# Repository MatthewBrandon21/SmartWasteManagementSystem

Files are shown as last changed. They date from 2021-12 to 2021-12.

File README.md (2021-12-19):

<h1 align="center">
  Smart Waste Management System (SWMS)
</h1>
<p align="center">
  Smart city waste management system for our Mobile Pervasive Computing course final project.
</p>

### Preview of this system
<p align="Center">
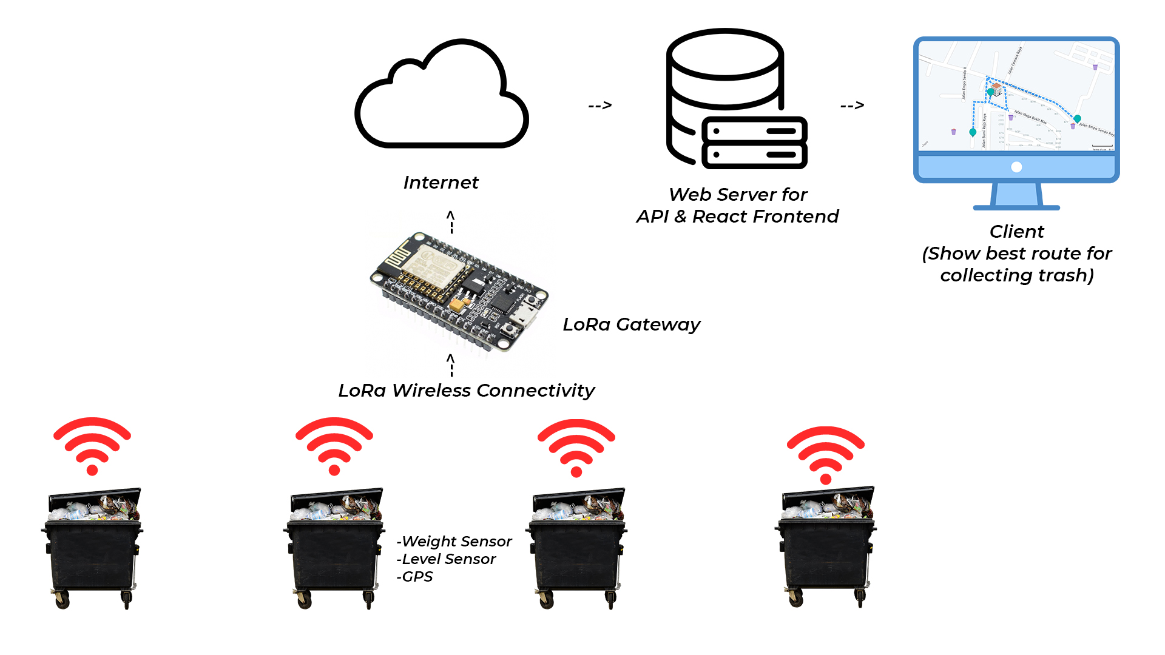
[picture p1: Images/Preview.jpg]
  
</p>

### General Architecture
<p align="Center">
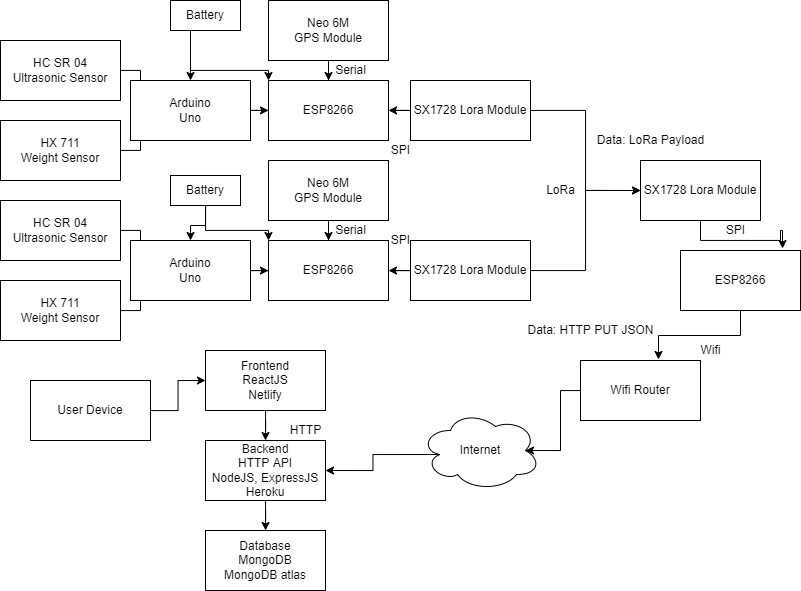
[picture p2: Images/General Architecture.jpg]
  
</p>

#

## How to make node device

### Hardware Architecture
<p align="Center">
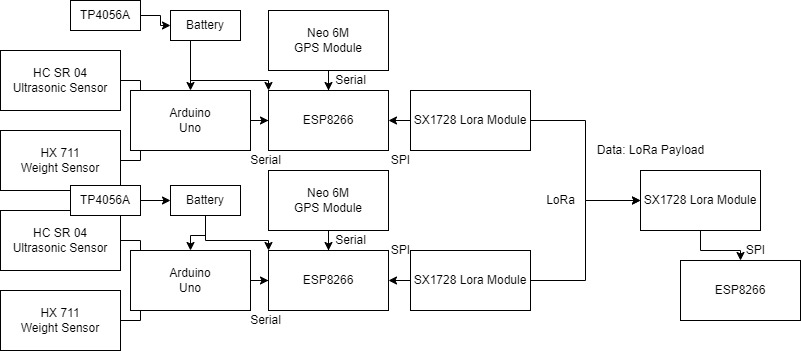
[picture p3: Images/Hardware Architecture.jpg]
  
</p>

### List of component
- Microcontroller ESP8266
- Microcontroller Arduino Uno
- Lora Module SX1278
- GPS Module Neo 6M
- Weight Sensor HX711+ 10kg Load cell
- Ultrasonic Sensor HC SR 04
- Servo SG40
- Battery 18650
- TP4056A

### List of component for gateway
- Microcontroller ESP8266
- Lora Module SX1278

Total budget (December 2021) = Rp. 356.200 (~ US $24,76)

### Component pin connection
1. Servo --> 
Orange : D3 (ESP8266),
Brown : GND (ESP8266),
Red : 3V3 (ESP8266)
2. Ultrasonic --> 
VCC : 5V (Arduino Uno),
Trig : Digital 5 (Arduino Uno),
Echo : Digital 6 (Arduino Uno),
GND : GND (Arduino Uno)
3. GPS --> 
GND : GND (ESP8266),
TX : D4 (ESP8266),
RX : D1 (ESP8266),
VCC : 3v3 (ESP8266)
4. HX711 --> 
VCC : 5V (Arduino Uno),
SCK : Digital 2 (Arduino Uno),
Data : Digital 3 (Arduino Uno),
GND : GND (Arduino Uno)
5. LoRa Wan --> 
GND : GND (ESP8266),
VCC : 3.3V (ESP8266),
NSS : D8 (ESP8266),
MOSI : D7 (ESP8266),
MISO : D6 (ESP8266),
CK : D5 (ESP8266),
RST : D0 (ESP8266),
DIO0 : D2 (ESP8266)
6. Serial Communication Arduino Uno and ESP8266 --> 
Digital 7 (Arduino Uno): TX (ESP8266),
Digital 8 (Arduino Uno): RX (ESP8266)

#

## How this work?
In this project, we use 2 microcontrollers, ESP8266 and Arduino Uno. The reason for using 2 microcontrollers simultaneously is because to supply power of weight sensor the HX711 module requires a larger current than the ESP8266 power regulator can provide. Therefore, if it is forced to run on esp8266, a bootloop will occur or it will restart continuously when the system boots. Arduino Uno's power regulator is larger than the ESP8266, therefore it can run the HX711 weight sensor module along with the ultrasonic sensor properly. But because we have implemented esp8266 in our prototype, we made it so that esp8266 and arduino uno can communicate to send sensor data. But if you want to save space, budget and efficiency, you can only use Arduino Uno.

For communication between the ESP8266 and Arduino Uno, use serial communication with a baud rate of 9600. Serial communication will happen every 3 seconds between Arduino Uno and Esp8266 to update esp8266 sensor data. And the lora frequency used is 915 MHz. To update data to API server will be done every 5 seconds by request by gateway. Then the gateway will request data one by one from the node so that data collisions do not occur (lora packet collosion -> for more details I have simulated packet collisions in LoRa communication which can be seen on).

For lora module with esp8266 using SPI communication protocol between the two. So the plot of Arduino Uno will send serial communication for weight sensor and Ultrasonic with plain text. Then it will be parsed by esp8266 in the trash, plus GPS data and the logic of whether the trash can is full or not by esp8266. And part of the value will be sent via Lora Payload to the esp8266 gateway. the gateway will parse the data sent by the node, and finally it will be generated as JSON to be sent HTTP PUT to the web API by the gateway.

<p align="Center">
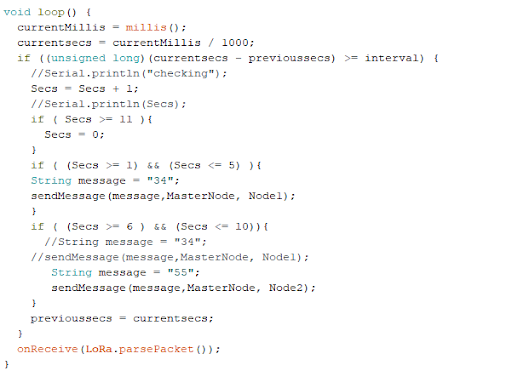
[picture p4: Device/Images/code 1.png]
  
</p>

So in the picture above, you can see the change in data retrieval requests and data updates to the API by the gateway. So in this example, seconds 1-5 will retrieve data from node 1 and seconds 6-10 will retrieve data from node 2.

#

## Final result
<p align="Center">
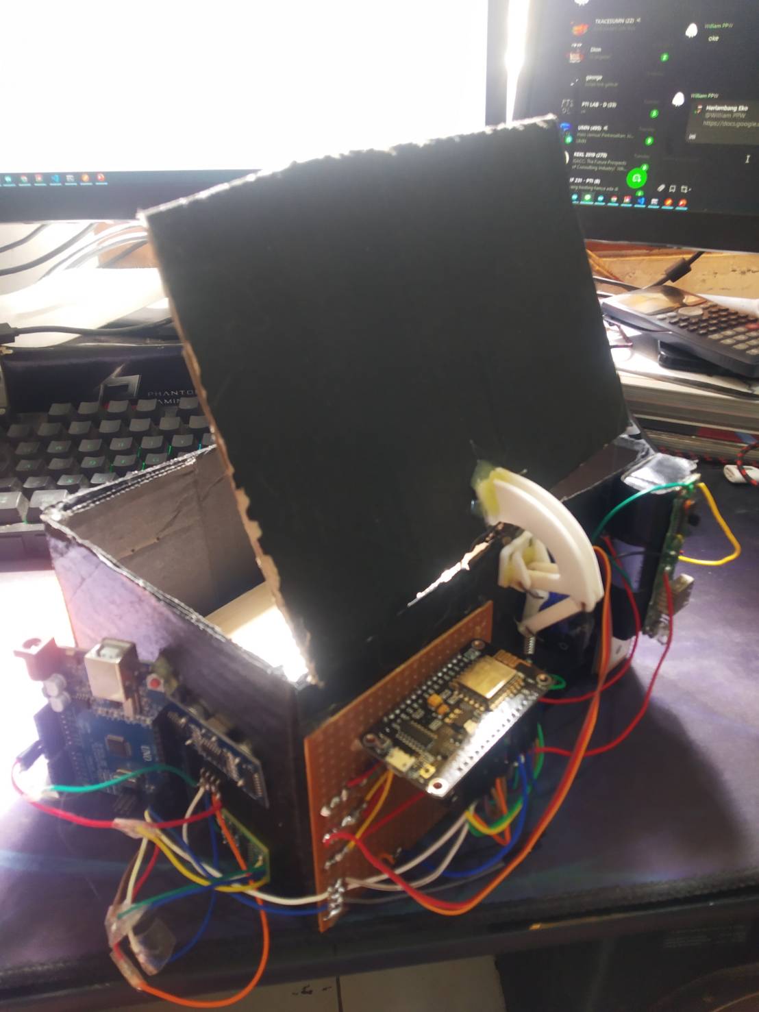
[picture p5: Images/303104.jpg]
  
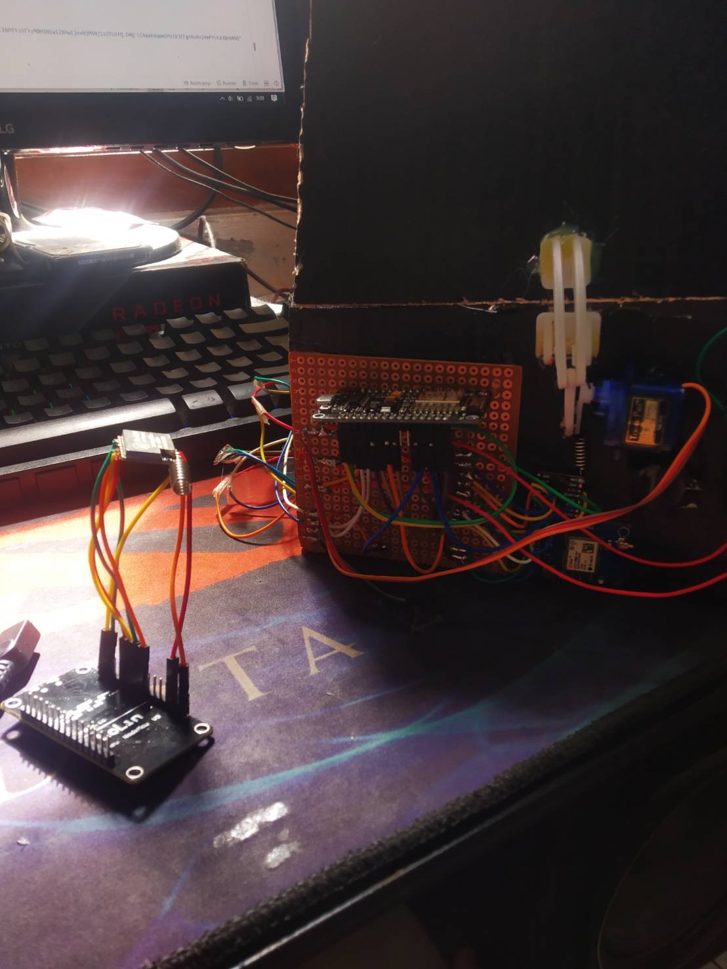
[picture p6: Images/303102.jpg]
  
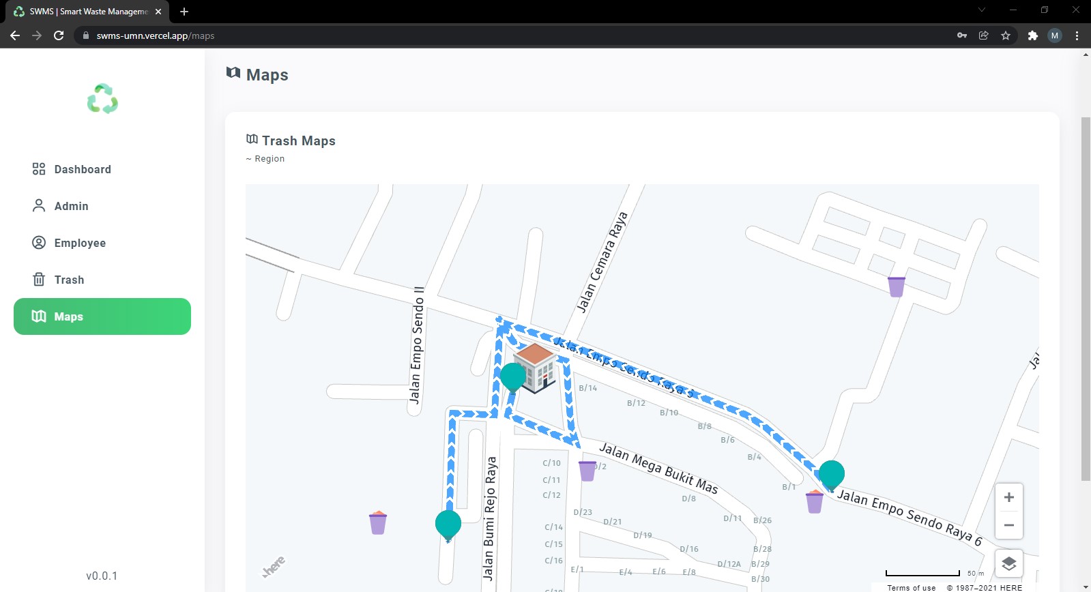
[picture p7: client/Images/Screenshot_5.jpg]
  
</p>

#

## <i>If need help, feel free to contact us! MatthewBrandon21 / rellpa.</i>

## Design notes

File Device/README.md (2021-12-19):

# Smart Waste Management System Arduino Code

We're using ESP8266
For some other controllers including controllers which are not ESP family, may need some more configuration.

#

## libraries
1. SPI.h
2. Lora.h
3. ESP8266WiFi.h
4. ESP8266HTTPClient.h
5. WiFiClient.h
6. TinyGPS++.h
7. SofwareSerial.h
8. Servo.h
9. HX711.h
10. stdlib.h

#

## How to use this project ?
If you want reverse engineering this project app:
- Install and open arduino IDE
- Install esp38266 board family, using board manager
- Clone and open "Arduino Uno.ino", "ESP8266 Gateway.ino", and "ESP8266 Node.ino"
- Configure URL of API Server on "ESP8266 Gateway.ino"
- Flash 3 ino file to seperate controller (Arduino Uno.ino --> arduino uno, ESP8266 Gateway.ino --> esp8266 gateway, etc)
- Done

#

## How this work?
In this project, we use 2 microcontrollers, ESP8266 and Arduino Uno. The reason for using 2 microcontrollers simultaneously is because to supply power of weight sensor the HX711 module requires a larger current than the ESP8266 power regulator can provide. Therefore, if it is forced to run on esp8266, a bootloop will occur or it will restart continuously when the system boots. Arduino Uno's power regulator is larger than the ESP8266, therefore it can run the HX711 weight sensor module along with the ultrasonic sensor properly. But because we have implemented esp8266 in our prototype, we made it so that esp8266 and arduino uno can communicate to send sensor data. But if you want to save space, budget and efficiency, you can only use Arduino Uno.

For communication between the ESP8266 and Arduino Uno, use serial communication with a baud rate of 9600. Serial communication will happen every 3 seconds between Arduino Uno and Esp8266 to update esp8266 sensor data. And the lora frequency used is 915 MHz. To update data to API server will be done every 5 seconds by request by gateway. Then the gateway will request data one by one from the node so that data collisions do not occur (lora packet collosion -> for more details I have simulated packet collisions in LoRa communication which can be seen on).

For lora module with esp8266 using SPI communication protocol between the two. So the plot of Arduino Uno will send serial communication for weight sensor and Ultrasonic with plain text. Then it will be parsed by esp8266 in the trash, plus GPS data and the logic of whether the trash can is full or not by esp8266. And part of the value will be sent via Lora Payload to the esp8266 gateway. the gateway will parse the data sent by the node, and finally it will be generated as JSON to be sent HTTP PUT to the web API by the gateway.

<p align="Center">
  
</p>

So in the picture above, you can see the change in data retrieval requests and data updates to the API by the gateway. So in this example, seconds 1-5 will retrieve data from node 1 and seconds 6-10 will retrieve data from node 2.

<i>if need help, feel free to contact us! MatthewBrandon21 / rellpa.</i>

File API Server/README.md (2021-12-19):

# Smart Waste Management System API
### <i>!!This app created using NodeJS and ExpressJS</i>

#

## Features:
- Store sensor data trash from node gateway to database
- Authentication user with JWT and have 2 user role (admin & employee, each user role have different privilege)
- CRUD user
- CRUD trashdata

#

## Library Dependencies
- @hapi/joi = Validation request input
- bcrypt.js = Hashing bcrypt algorithm
- cors = Middleware for ExpressJS for HTTP header based
- dotenv = Make and use .env file
- express.js = HTTP framwork for NodeJS
- jsonwebtoken = untuk authentukasi dan authorisasi
- mongoose = Framework to use MongoDB database
- nanoid = MongoDB ObjectID generator. Shortener objectID length.
- nodemon : Development tool for auto restarting NodeJS 

#

## Demo app:
You can access this demo API to https://smartwastemanagement-api.herokuapp.com/

#

## How to use this project ?
If you want reverse engineering this project app:
1. Clone this folder
2. Make MongoDB database with users and trashdatas collection (You can see example on JSON Database/ .json).
2. Set url mongoDB database in config/db.config.js
3. set port according to your system port availability in app.js 
4. Run npm install
5. Run npm run

How to use API:
1. You must register first, use register POST method
2. Login with account that you have created, use login POST method
3. In the login response there is a JWT token that will expire in 1 hour
4. Copy and paste that JWT token as POST method header, Header key named "auth-token" with value JWT token

<i>if need help, feel free to contact us! MatthewBrandon21 / rellpa.</i>

#

## API Documentation
Trash data API ( /trashdata):
- router.get("/",trashdata.findAll);  -> Get all trash data

- router.post("/", trashdata.create); -> Make new trash data (use json body on http request)

- router.get("/:id", trashdata.findOne); -> Get trash data by id

- router.put("/:id", trashdata.update); -> Update trash data by id (use json body on http request)

- router.delete("/:id",trashdata.delete); -> Delete trash data by id

API User :
- router.get("/", users.findAll); -> Get all users
 
- router.get("/:id", users.findOne); -> Get a user by id

- router.put("/:id", users.update); -> Update user by id (use json body on http request)
 
- router.delete("/:id", users.delete); -> Delete user by id
 
- router.post("/register", async (req, res) => { function goes here } -> Register user
 
- router.post("/login", async (req, res) => { function goes here } -> Login user

#

### <i>*For improvement<i/>
You can add authentication for device (ESP32 HTTP POST)

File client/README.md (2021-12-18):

# Smart Waste Management System Frontend
### <i>!!This app created using ReactJS and HERE Routing API</i>

#

## Features:
- Dashboard page
- Login page
- Responsive web page
- CRUD admin user
- CRUD employee user
- CRUD Trash
- Auto map routing based trash --> Using HERE Routing API

#

## Demo app:
You can access this demo web to https://swms-umn.vercel.app/
For demo account:
Admin--> email: william@gmail.com password: 12345678
Employee--> email: pervasif@gmail.com password: pervasifsukses

#

## How to use this project ?
If you want reverse engineering this project app:
1. Clone this folder
2. Set Smart Waste Management System API Server url in src/api/index.jsx
3. Run npm install
4. Run npm run

<i>if need help, feel free to contact us! MatthewBrandon21 / rellpa.</i>

#

## Some Screenshoot of this web
<p align="left">
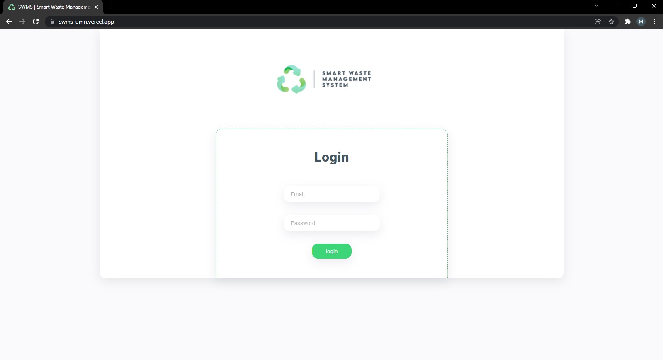
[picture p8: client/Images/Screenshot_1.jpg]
  
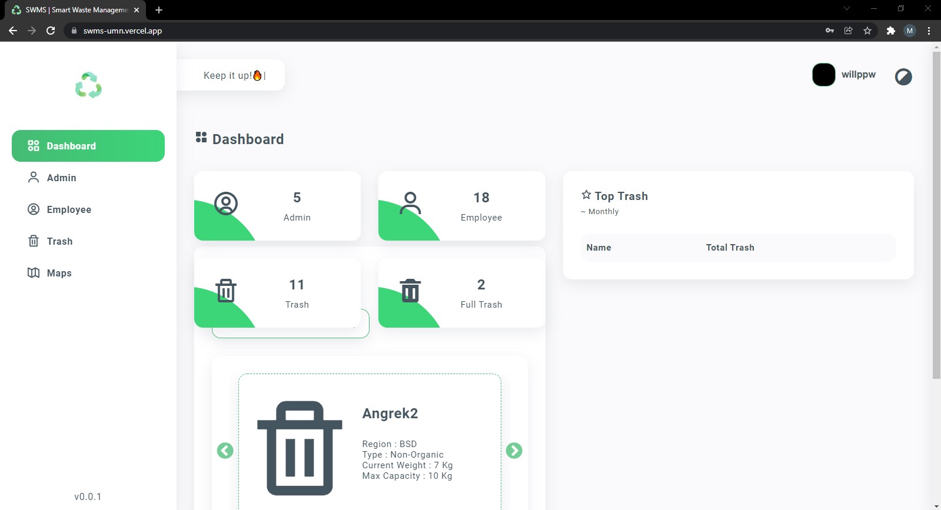
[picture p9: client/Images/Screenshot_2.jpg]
  
  
</p>

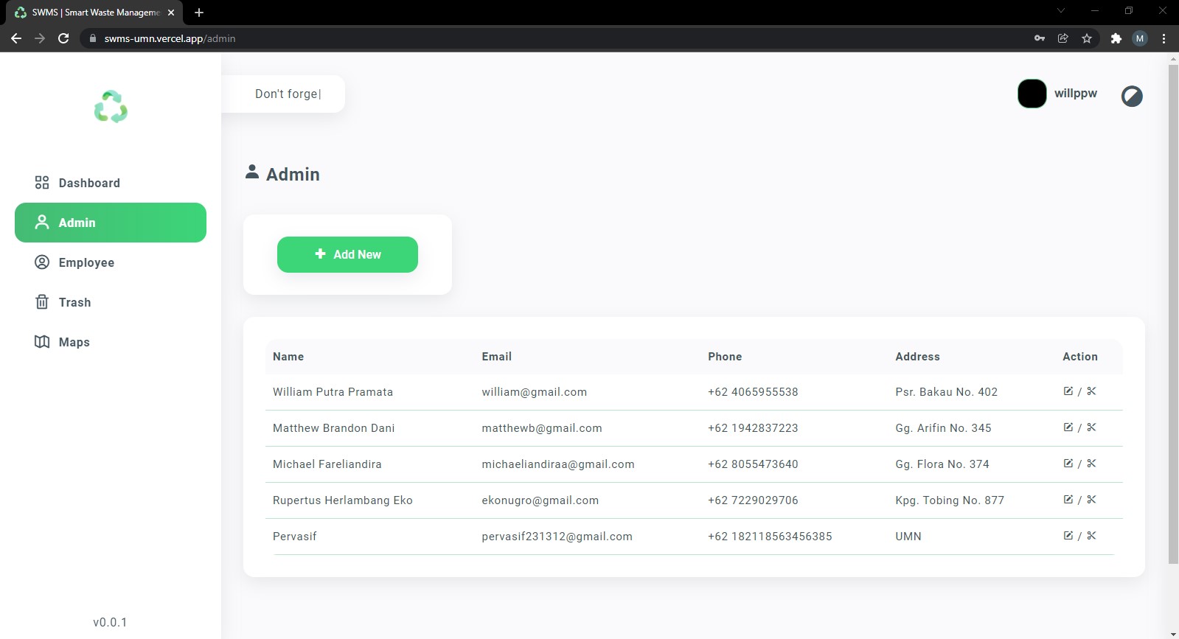
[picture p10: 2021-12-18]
client/Images/Screenshot_3.jpg

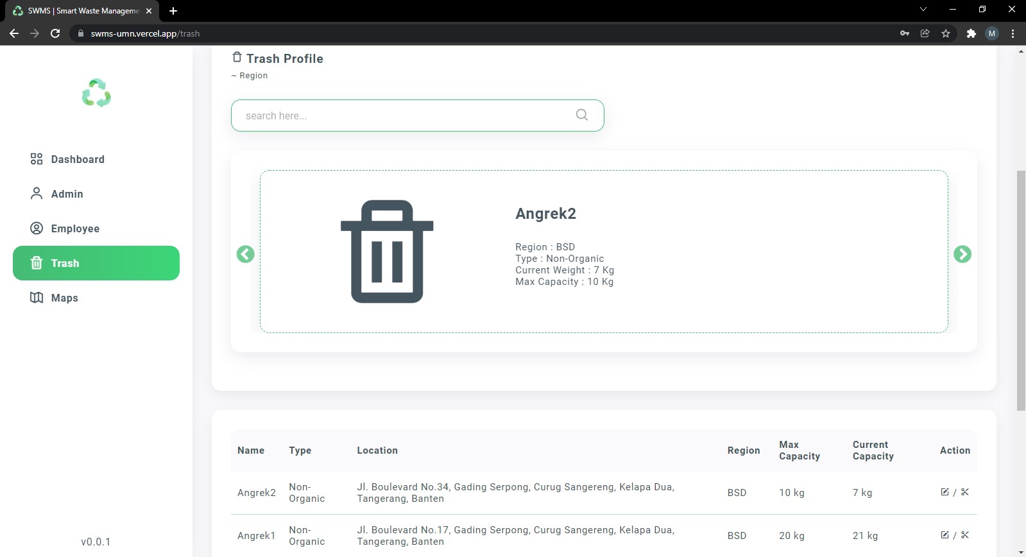
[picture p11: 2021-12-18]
client/Images/Screenshot_4.jpg

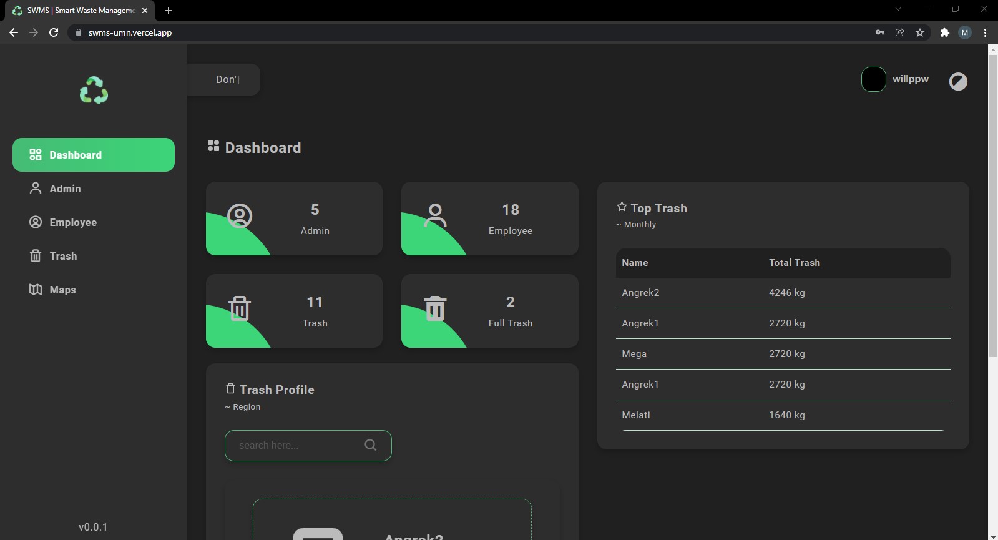
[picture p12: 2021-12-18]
client/Images/Screenshot_6.jpg

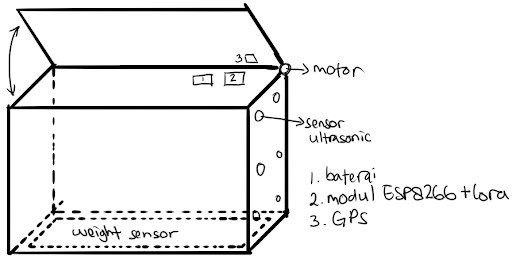
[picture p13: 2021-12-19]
Images/Plan.png

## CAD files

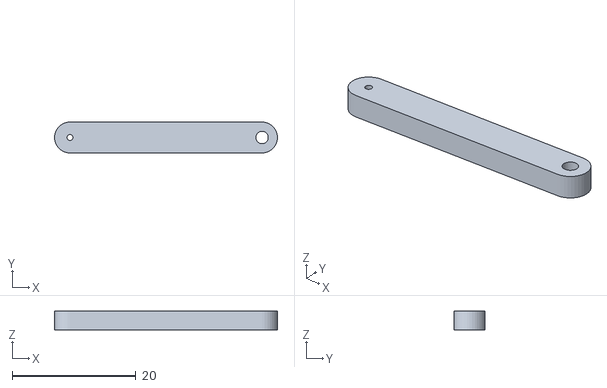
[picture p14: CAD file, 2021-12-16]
Device/3D Print for Servo Hinge/Push_Rod.STL
36.0 x 5.00 x 3.00

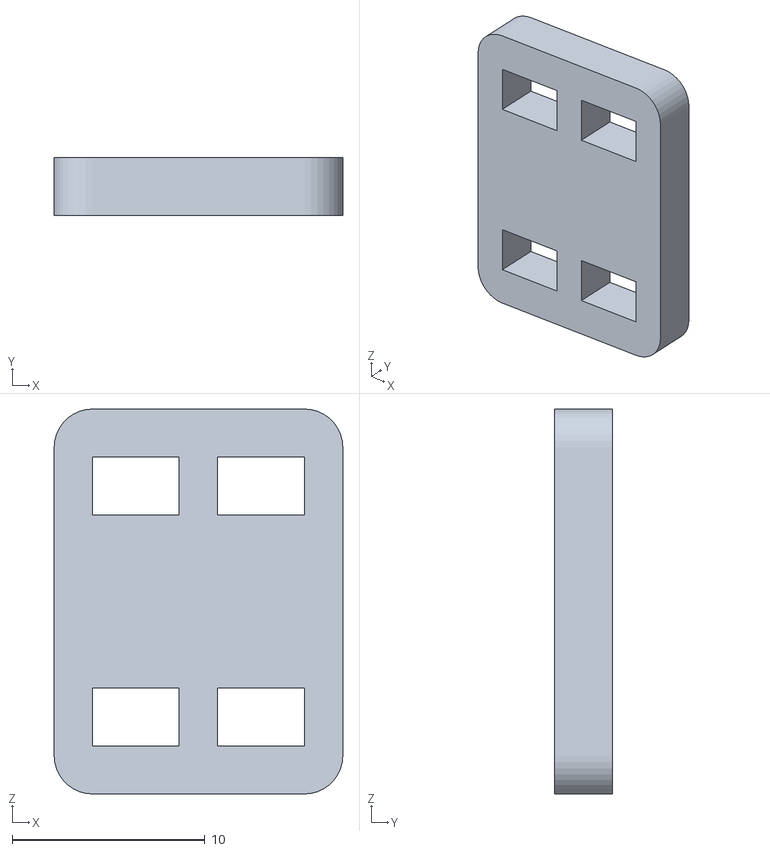
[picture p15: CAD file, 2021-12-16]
Device/3D Print for Servo Hinge/Hinge_Base.STL
15.0 x 3.00 x 20.0

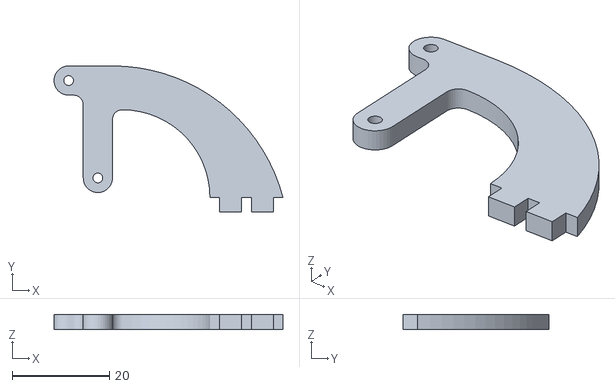
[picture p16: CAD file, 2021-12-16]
Device/3D Print for Servo Hinge/Horn.STL
47.0 x 30.0 x 3.00

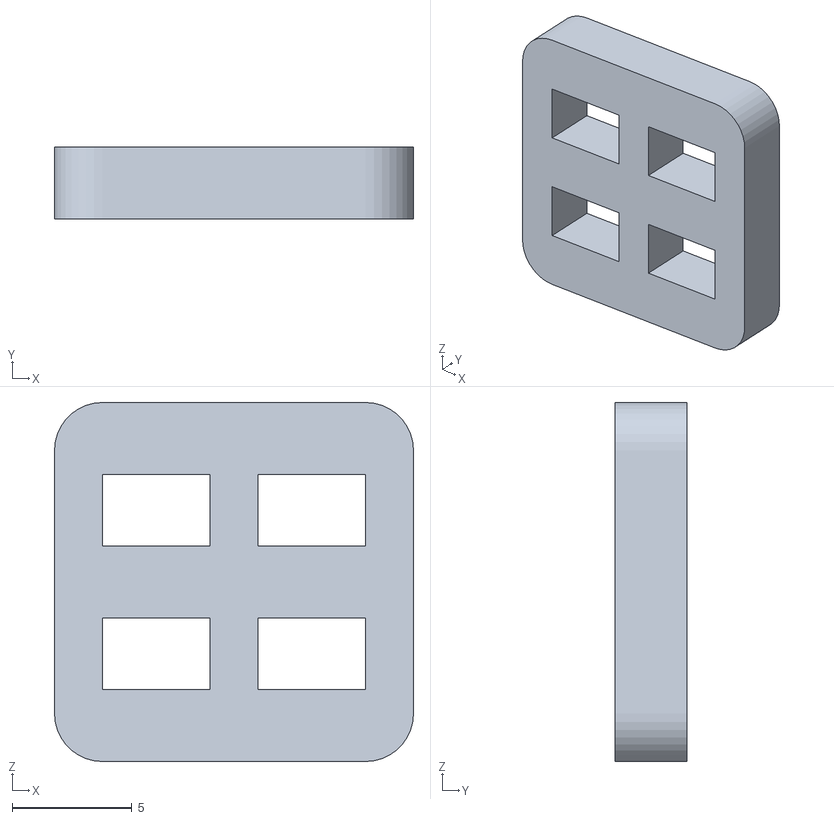
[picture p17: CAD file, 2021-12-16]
Device/3D Print for Servo Hinge/Horn_Base.STL
15.0 x 3.00 x 15.0

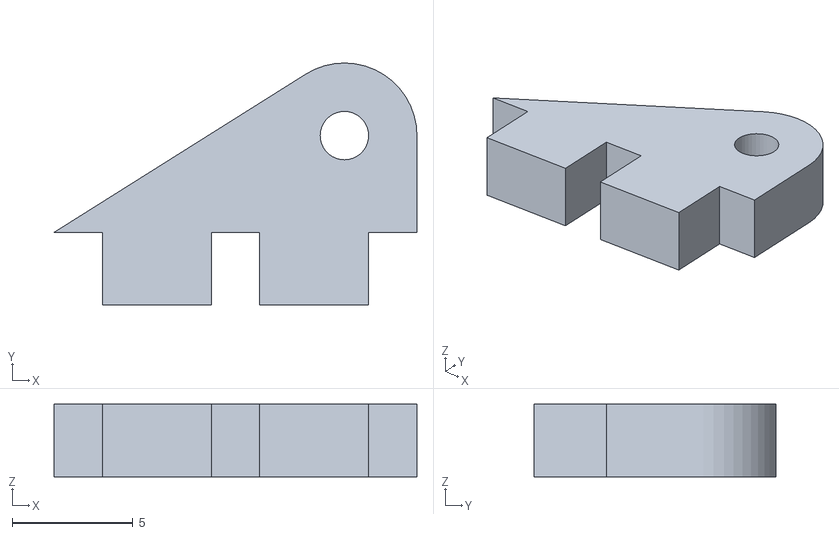
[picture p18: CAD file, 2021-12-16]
Device/3D Print for Servo Hinge/Hinge.STL
15.0 x 10.00 x 3.00

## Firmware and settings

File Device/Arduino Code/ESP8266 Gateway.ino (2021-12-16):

#include <SPI.h>
#include <LoRa.h>
#include <ESP8266WiFi.h>
#include <ESP8266HTTPClient.h>
#include <WiFiClient.h>

#define ss 15
#define rst 16
#define dio0 2

const char* ssid = "WiskaTimmy";
const char* password = "asukabeh";
const char* serverName = "http://smartwastemanagement-api.herokuapp.com/trashdata/";
 
byte MasterNode = 0xFF;
byte Node1 = 0xBB;
byte Node2 = 0xCC;

String SenderNode = "";
String outgoing;
String incoming;
String weightsval;
String levelval;
String latval;
String lonval;
String fullval;
String idval;
String json;

byte msgCount = 0;

// Tracks the time since last event fired
unsigned long previousMillis=0;
unsigned long int previoussecs = 0;
unsigned long int currentsecs = 0;
unsigned long currentMillis = 0;
int interval= 5 ; // updated every 5 second
int Secs = 0;


void setup() {
  Serial.begin(115200);
  WiFi.begin(ssid, password);
  Serial.println("Connecting");
  while(WiFi.status() != WL_CONNECTED) {
    delay(500);
    Serial.print(".");
  }
  Serial.println("");
  Serial.print("Connected to WiFi network with IP Address: ");
  Serial.println(WiFi.localIP());
  Serial.println("LoRa Receiver master");
  LoRa.setPins(ss, rst, dio0);
  if (!LoRa.begin(433E6)) {          // initialize ratio at 915 MHz
    Serial.println("LoRa init failed. Check your connections.");
    while (true);
  }
  Serial.println("LoRa init succeeded.");
}

void loop() {
  currentMillis = millis();
  currentsecs = currentMillis / 1000; 
  if ((unsigned long)(currentsecs - previoussecs) >= interval) {
    //Serial.println("checking");
    Secs = Secs + 1;
    //Serial.println(Secs);
    if ( Secs >= 11 ){
      Secs = 0; 
    }
    if ( (Secs >= 1) && (Secs <= 5) ){
    String message = "34"; 
    sendMessage(message,MasterNode, Node1);
    }
    if ( (Secs >= 6 ) && (Secs <= 10)){
      String message = "34"; 
    sendMessage(message,MasterNode, Node1);
    //   String message = "55"; 
    //   sendMessage(message,MasterNode, Node2);
    }
    previoussecs = currentsecs;
  }
  onReceive(LoRa.parsePacket());
}


void sendMessage(String outgoing, byte MasterNode, byte otherNode) {
  LoRa.beginPacket();                   // start packet
  LoRa.write(otherNode);                // add destination address
  LoRa.write(MasterNode);               // add sender address
  LoRa.write(msgCount);                 // add message ID
  LoRa.write(outgoing.length());        // add payload length
  LoRa.print(outgoing);                 // add payload
  LoRa.endPacket();                     // finish packet and send it
  msgCount++;                           // increment message ID
}

void onReceive(int packetSize) {
  //Serial.println("LoRa receive.");
  if (packetSize == 0){
    return;          // if there's no packet, return
  }
  // read packet header bytes:
  int recipient = LoRa.read();          // recipient address
  byte sender = LoRa.read();            // sender address
  if( sender == 0XBB )
    SenderNode = "Node1:";
  if( sender == 0XCC )
    SenderNode = "Node2:";
  byte incomingMsgId = LoRa.read();     // incoming msg ID
  byte incomingLength = LoRa.read();    // incoming msg length

  incoming = "";

  while (LoRa.available()) {
    incoming += (char)LoRa.read();
  }

  if (incomingLength != incoming.length()) {   // check length for error
    Serial.println("error: message length does not match length");
    ;
    return;                             // skip rest of function
  }

  // if the recipient isn't this device or broadcast,
  if (recipient != Node1 && recipient != MasterNode) {
   Serial.println("This message is not for me.");
    ;
    return;                             // skip rest of function
  }
  Serial.println("check success");
  
  weightsval = getValue(incoming, ',', 0); // weight
  levelval = getValue(incoming, ',', 1); // level
  latval = getValue(incoming, ',', 2); // lat
  lonval = getValue(incoming, ',', 3); // lon
  fullval = getValue(incoming, ',', 4); // full
  idval = getValue(incoming, ',', 5); // id

 if( sender == 0xBB ){ 
  Serial.println(incoming + " From node 1");
  Serial.println("weight:" + weightsval);
  Serial.println("level:" + levelval);
  Serial.println("lat:" + latval);
  Serial.println("lon:" + lonval);
  Serial.println("isfull:" + fullval);
  Serial.println("id:" + idval);
 }

  if( sender == 0xCC ){ 
  Serial.println(incoming + " From node 2");
  Serial.println("weight:" + weightsval);
  Serial.println("level:" + levelval);
  Serial.println("lat:" + latval);
  Serial.println("lon:" + lonval);
  Serial.println("isfull:" + fullval);
  Serial.println("id:" + idval);
 }
 sendtoapi();
 incoming = "";
}

String getValue(String data, char separator, int index){
    int found = 0;
    int strIndex[] = { 0, -1 };
    int maxIndex = data.length() - 1;
 
    for (int i = 0; i <= maxIndex && found <= index; i++) {
        if (data.charAt(i) == separator || i == maxIndex) {
            found++;
            strIndex[0] = strIndex[1] + 1;
            strIndex[1] = (i == maxIndex) ? i+1 : i;
        }
    }
    return found > index ? data.substring(strIndex[0], strIndex[1]) : "";
}

void sendtoapi(){
  if(WiFi.status()== WL_CONNECTED){
    WiFiClient client;
    HTTPClient http;
    String path = serverName+idval;
    Serial.println(path);
    http.setTimeout(15000);
    http.begin(client, path);
    http.addHeader("Content-Type", "application/json");
    if( fullval.toInt() == 1){
      json = "{\"tempat_sampah_current\": {\"tempat_sampah_gpslocation\": {\"lon\": " + lonval + ",\"lat\": " + latval + "},\"tempat_sampah_currentcapacity\": " + weightsval + ",\"tempat_sampah_currentlevel\": " + levelval + "},\"tempat_sampah_isfull\": true}";
    }else{
      json = "{\"tempat_sampah_current\": {\"tempat_sampah_gpslocation\": {\"lon\": " + lonval + ",\"lat\": " + latval + "},\"tempat_sampah_currentcapacity\": " + weightsval + ",\"tempat_sampah_currentlevel\": " + levelval + "},\"tempat_sampah_isfull\": false}";
    }
    Serial.println(json);
    int httpResponseCode = http.PUT(json);
    Serial.print("HTTP Response code: ");
    Serial.println(httpResponseCode);
    http.end();
  } else {
      Serial.println("WiFi Disconnected");
  }
}

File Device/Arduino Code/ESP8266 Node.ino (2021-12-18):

#include <SPI.h>
#include <LoRa.h>
#include <TinyGPS++.h>
#include <SoftwareSerial.h>
#include <Servo.h>

#define ss 15
#define rst 16
#define dio0 2

TinyGPSPlus gps;
SoftwareSerial ssgps(D4, D1);
Servo servo;

int weightvalue;
int levelvalue;
int firstVal;
int full = 0;
String outgoing;
String lat_str = "-7.085588";
String lon_str = "110.417997";
String myString;
String nodemessage = "";
String idnode = "amQ";
String weight;
String level;
char rdata;
byte msgCount = 0;
byte MasterNode = 0xFF;
byte Node1 = 0xBB;
float latitude , longitude;

void setup() {
  Serial.begin(115200);
  ssgps.begin(9600);
  while (!Serial);
  Serial.println("LoRa Duplex");
  LoRa.setPins(ss, rst, dio0);
  if (!LoRa.begin(433E6)) {             // initialize ratio at 915 MHz
    Serial.println("LoRa init failed. Check your connections.");
    while (true);
  }
  Serial.println("LoRa init succeeded.");
  servo.attach(0); //D4
}

void loop() {
  if (Serial.available() > 0 ) {
    rdata = Serial.read(); 
    myString = myString+ rdata; 
    if( rdata == '\n'){
      Serial.println(myString);
      weight = getValue(myString, ',', 0);
      weightvalue = weight.toInt(); 
      Serial.println(weight + "," + weightvalue);
      level = getValue(myString, ',', 1);
      levelvalue = level.toInt(); 
      Serial.println(level + "," + levelvalue);
      myString = "";
    }
  }
  while (ssgps.available() > 0){
      if (gps.encode(ssgps.read())){
       if (gps.location.isValid()){
         latitude = gps.location.lat();
         lat_str = String(latitude , 6);
         Serial.println(lat_str);
         longitude = gps.location.lng();
         lon_str = String(longitude , 6);
         Serial.println(lon_str);
       }
    }
  }
  if (weightvalue >= 1 || levelvalue <=15 && levelvalue != 0){
    full = 1;
    servo.write(0);
  } else {
    full = 0;
    servo.write(45);
  }
  onReceive(LoRa.parsePacket(), weightvalue, levelvalue, full);
  //nodemessage = String(weightvalue) +"," + String(levelvalue) + "," + lat_str + "," + lon_str + "," + full + "," + idnode; 
  //Serial.println(nodemessage);
}

void sendMessage(String outgoing, byte MasterNode, byte otherNode) {
  LoRa.beginPacket();                   // start packet
  LoRa.write(MasterNode);               // add destination address
  LoRa.write(Node1);                    // add sender address
  LoRa.write(msgCount);                 // add message ID
  String massagenodeini = String(weightvalue) +"," + String(levelvalue) + "," + lat_str + "," + lon_str + "," + full + "," + idnode;
  LoRa.write(outgoing.length());        // add payload length
  LoRa.print(outgoing);                 // add payload
  Serial.println(outgoing);
  LoRa.endPacket();                     // finish packet and send it
  msgCount++;                           // increment message ID
  massagenodeini = "";
}

void onReceive(int packetSize, int wv, int lv, int f) {
  if (packetSize == 0) return;
  int recipient = LoRa.read();          // recipient address
  byte sender = LoRa.read();            // sender address
  byte incomingMsgId = LoRa.read();     // incoming msg ID
  byte incomingLength = LoRa.read();    // incoming msg length
  String incoming = "";
  while (LoRa.available()) {
    incoming += (char)LoRa.read();
  }
  if (incomingLength != incoming.length()) {   // check length for error
   Serial.println("error: message length does not match length");
   ;
    return;                             // skip rest of function
  }
  // if the recipient isn't this device or broadcast,
  if (recipient != Node1 && recipient != MasterNode) {
    Serial.println("This message is not for me.");
    ;
    return;                             // skip rest of function
  }
    Serial.println("check success");
    Serial.println(incoming);
    int Val = incoming.toInt();
    if(Val == 34){ 
      nodemessage = "";
      nodemessage = nodemessage + String(wv) +"," + String(lv) + "," + lat_str + "," + lon_str + "," + f + "," + idnode; 
      sendMessage(nodemessage,MasterNode,Node1);
      Serial.println("massage sent");
      nodemessage = "";
      delay(100);
    }
}

String getValue(String data, char separator, int index){
    int found = 0;
    int strIndex[] = { 0, -1 };
    int maxIndex = data.length() - 1;

    for (int i = 0; i <= maxIndex && found <= index; i++) {
        if (data.charAt(i) == separator || i == maxIndex) {
            found++;
            strIndex[0] = strIndex[1] + 1;
            strIndex[1] = (i == maxIndex) ? i+1 : i;
        }
    }
    return found > index ? data.substring(strIndex[0], strIndex[1]) : "";
}
